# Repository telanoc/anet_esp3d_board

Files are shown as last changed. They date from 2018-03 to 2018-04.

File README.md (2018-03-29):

anet_esp3d_board
Copyright (c) 2018 by Pete Cervasio <cervasio@airmail.net>

License: Creative Commons Attribution-ShareAlike 4.0 International
(CC BY-SA 4.0)

This project implements a board to plug an ESP-01 running the ESP3d
software into the extra 10-pin connector on the Anet controller.

The transmit data of the ESP-01 is passed through a gated buffer, so that
GPIO 0 must be brought low for data to be sent to the printer.  This keeps
the ESP8266 startup noise out of the printer so it doesn't cough up a fur
ball.

You must remove two zero ohm resistors from the controller.  R52 and R53.
You must also either solder on a 6-pin jumper header or just solder jumper
wires in the BLE position of the USB/BLE pins.

Since GPIO 0 needs to be brought low, you must modify setup() of the ESP3d
sketch to add the following two lines:

void setup() {
    ... existing stuff

	pinMode(0, OUTPUT);
	digitalWrite(0, LOW);

	... more existing stuff

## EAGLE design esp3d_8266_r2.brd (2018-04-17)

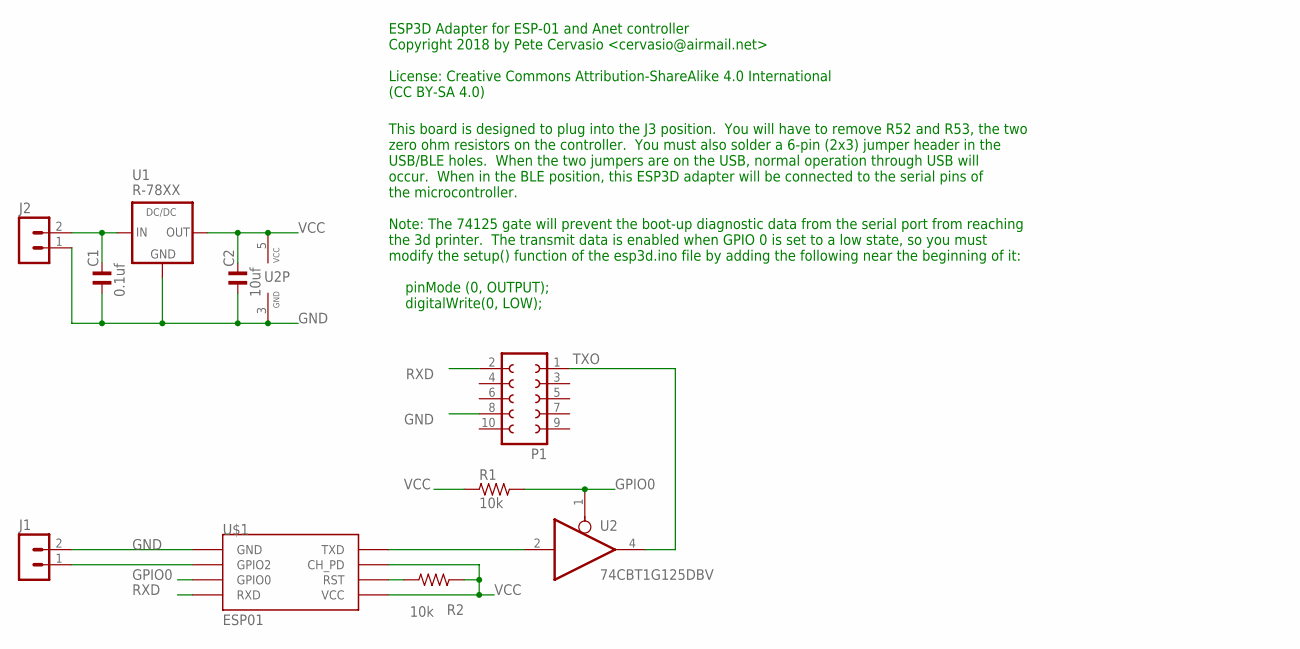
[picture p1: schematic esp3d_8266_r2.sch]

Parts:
C1: 0.1uf; C0805
C2: 10uf; C0805
J1, J2: MA02-1
P1: FE05-2
R1, R2: 10k; R0805
U1: R-78XX
U2: 74CBT1G125DBV; SOT23-5
U$1: ESP01

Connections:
GND: C1.1, C2.1, J1.2, J2.1, P1.8, U1.2 (GND), U2.3 (GND), U$1.GND
GPIO0: R1.2, U2.1 (OE), U$1.GPIO0
unnamed: U2.2 (I), U$1.TX (TXD)
unnamed: R2.2, U$1.RST
unnamed: J1.1, U$1.GPIO2
unnamed: C1.2, J2.2, U1.1 (IN)
RXD: P1.2, U$1.RX (RXD)
TXO: P1.1, U2.4 (O)
VCC: C2.2, R1.1, R2.1, U1.3 (OUT), U2.5 (VCC), U$1.CH_PD, U$1.VCC

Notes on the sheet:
ESP3D Adapter for ESP-01 and Anet controller Copyright 2018 by Pete Cervasio <cervasio@airmail.net> License: Creative Commons Attribution-ShareAlike 4.0 International (CC BY-SA 4.0)
This board is designed to plug into the J3 position. You will have to remove R52 and R53, the two zero ohm resistors on the controller. You must also solder a 6-pin (2x3) jumper header in the USB/BLE holes. When the two jumpers are on the USB, normal operation through USB will occur. When in the BL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

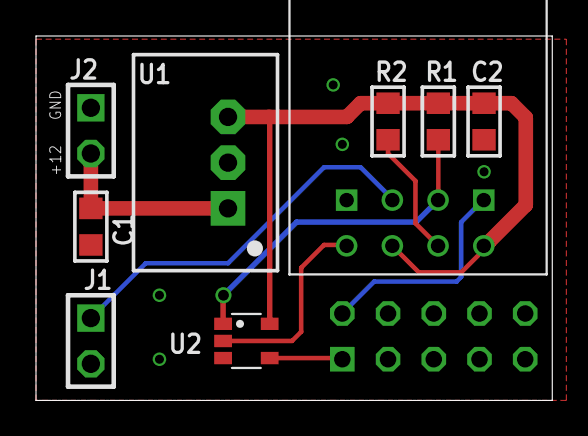
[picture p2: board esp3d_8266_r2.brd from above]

Board: 2 copper layers, 28.7 x 20.2 mm, 10 parts (1 on the bottom side), 9 nets.

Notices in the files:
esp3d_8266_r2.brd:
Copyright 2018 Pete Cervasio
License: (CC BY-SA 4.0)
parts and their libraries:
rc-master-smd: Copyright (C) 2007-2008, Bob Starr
